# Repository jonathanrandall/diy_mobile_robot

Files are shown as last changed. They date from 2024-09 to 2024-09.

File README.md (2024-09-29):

# DIY Mobile Robotics Platform:
The video instructions are [here](https://youtu.be/9S9H8HX5MNA). <br/>
The regression used to calibrate the stereo camera is in the file __points_regression.ods__. <br/>
The fritzing diagram for the pcb is in __esp32_motor_control.fzz__ <br/>
The gerber files for the pcb are in __gerber_esp32_motor_control__ <br/>
The code is in [robot_software](https://github.com/jonathanrandall/diy_mobile_robot/tree/main/robot_software). <br/>
Robot software depends on [cvzone library](https://github.com/cvzone/cvzone).

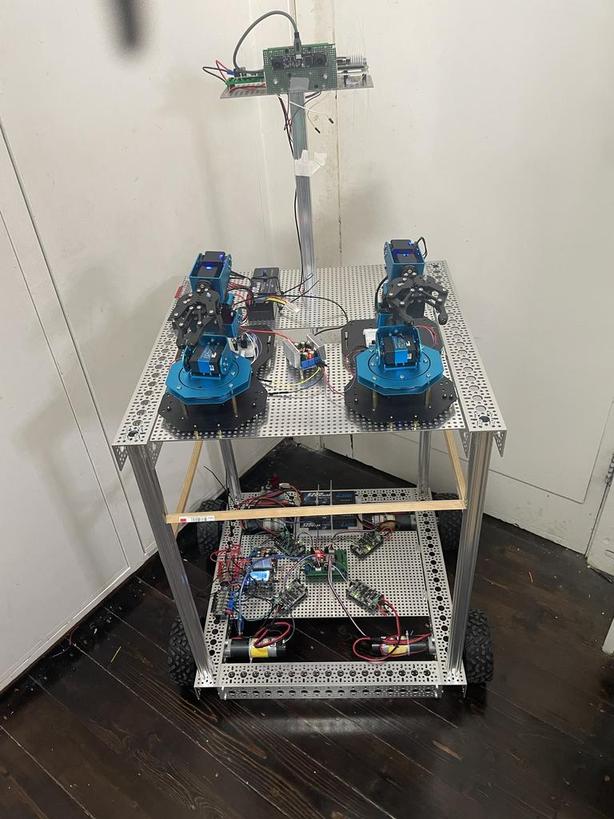
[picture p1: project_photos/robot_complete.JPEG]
the robot


# Assemble the Frame and Motors.

__Screw Drivers and Hex Keys__<br/>
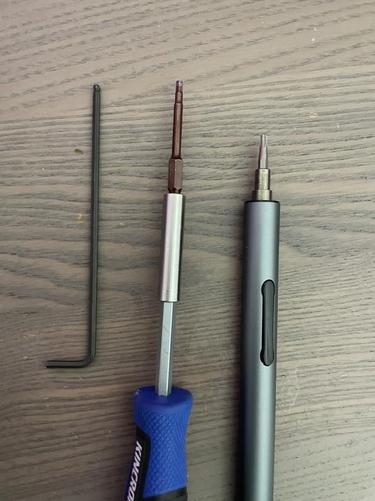
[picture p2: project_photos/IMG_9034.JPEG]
screw drivers
 <br/>
The M4 socket head screws require a 3mm drive size. It is recommended to get the __Wera Tools 3mm Ball-End Hex-Plus L-Key__ (SKU: 5027104001). This will make building much easier, since it can access screws in awkward places. The drivers I used are pictured below.

__Step 1: Build the base of the frame:__<br/>
Note: robot upside down in picutre, so base is at the top. <br/>
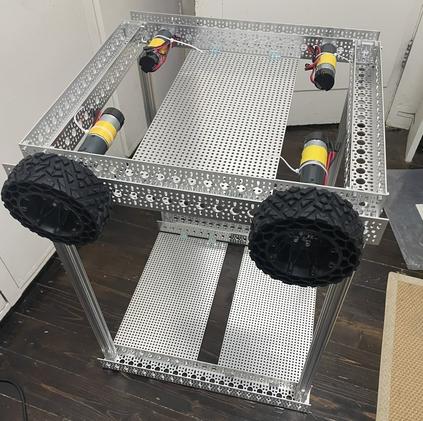
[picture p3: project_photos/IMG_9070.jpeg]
robot frame
<br/>
<ins>parts list for base</ins>
* 2 X 432mm 1120 Series U-Channel (SKU: 1120-0017-0432)
* 2 X 528mm 1120 Series U-Chaneel (SKU: 1120-0021-0528)
* 4 X 1201 Series Quadblock pattern mount (SKU: 1201-0043-0002)
* 16 X 11mm M4 screws
* 16 X 8mm M4 screws
* 16 X 12mm M4 screws
* 4 X flanged ball bearing, 8mm REX ID x 14mm OD, 5mm thickness (SKU: 1611-0514-4008). Note ID is inner diameter and OD is outer diameter.
* 4 X 1320 Series hyper hub, 8mm REX Bore (SKU: 1310-0016-4008)
* 4 X Threaded Steel L-Bracket, 3 hole (SKU: 1147-0001-0003). Note there are four in each pack, so once pack.
* 1 X 1116 Series Grid Plate, 29 x 53 Hole, 232 x 424mm (SKU: 1116-0232-0424)
* 24 X 6mm screws (can also use 8mm if you run out, but 6mm is preferred).
* 5204 Series Yellow  Jacket Planetary Gear Motor, 80mm Lenght 8mm REX shart, 117 RPM (SKU: 5204-8002-0051). Note, this is the long shaft motor. If you use the shorter shaft, you will need a coupler and a shaft to attach to the wheel. This can be quite fiddly and adds to the cost. Also I'm using the 117 RPM motor, which is not fast but has good torque. My aim is to handle a payload of up to 50kg on a 30 degree incline. According to my calculations, this should handle that quite well, but might struggle witht he 223 RMP version.
* 4 X 1109 Series goRail, 624mm lenghth (SKU: 1109-0024-0624). 

<ins>Assembly of base</ins>
1. Attach the quadblocks to the end of the shorter U-channels (432mm) with the 11mm screws. Mounting the quadblocks on the shorter channels will result in the base being a square. Each channel is 48mm wide, so the base will be (432 +48 +48) = 528mm. Note, you can use different sized U-Channels, depending on what you need. I've chosen theses sizes to bring it into line with the Stanford Mobile Aloha robot. This build is on the wider end of what I would normally do.<br/> 
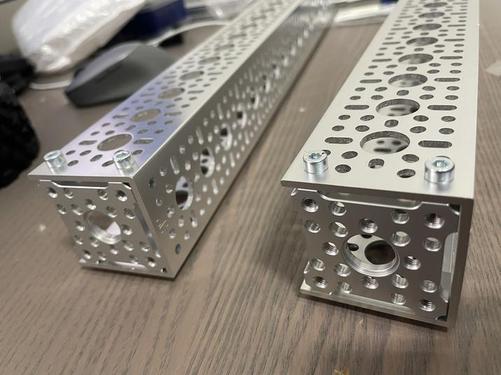
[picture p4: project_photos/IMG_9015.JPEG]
Quad Blocks

2. Attach the two 432mm at right angles with the 528mm channels, using the 8mm screws to connect, to make a square shape (see picture).<br/>
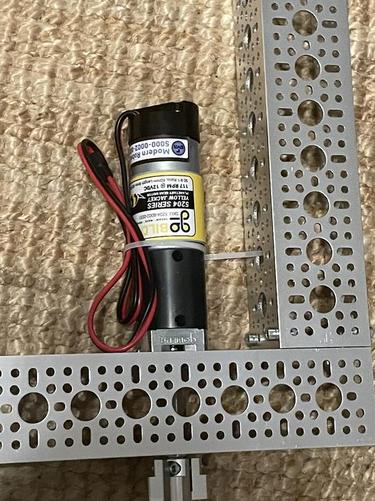
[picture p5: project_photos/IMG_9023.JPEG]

3. Attach the motors to the side of the frame. You can 10mm to 12mm screws for this. I've attached mine to the fourth hole down. There are lots of diagrams on the gobilda page for attaching the motors to channel. Make sure the motor's power wires and encoder plug are facing upwards, so they are easy to access from the top. <br/>
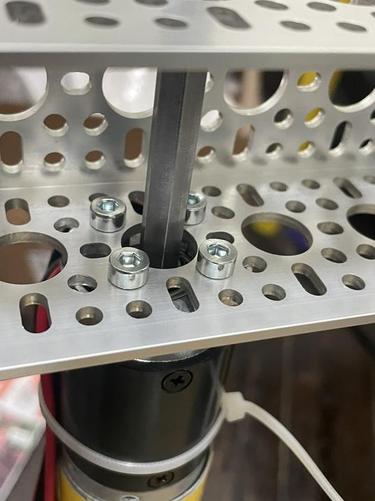
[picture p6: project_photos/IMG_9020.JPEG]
motor attach

4. Place the bearing,spacer and hyperhub on the end of the motor shaft and push down so that everything is nice and snug. Tighten the pinch screws on the hyperhub. Don't place the wheels on yet. They will get in the way.<br/>
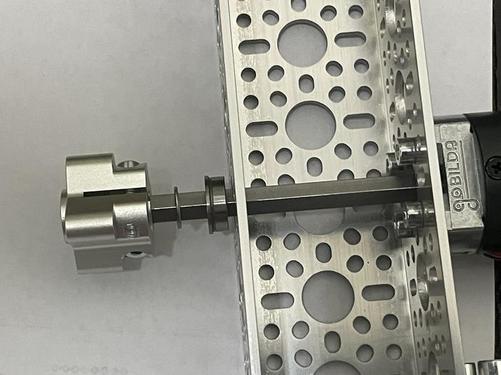
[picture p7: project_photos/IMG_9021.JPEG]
bearing attach

5. Attach the goRail to the corners of the base with the 12mm M4 screws (or 10mm is ok as well), so they are standing verticle. They have threaded holes, which will line up with the holes on the U-Channel. When you attach a goRail, do not tighten the screws until all four have been placed, otherwise you risk cross-threading. I'm using 624mm goRail. You can use up to 1200mm. You can adjust the height of the goRail without changing anything else. If you adjust the dimensions of the U-Channel, the grid plates will also need to be adjusted.<br/>
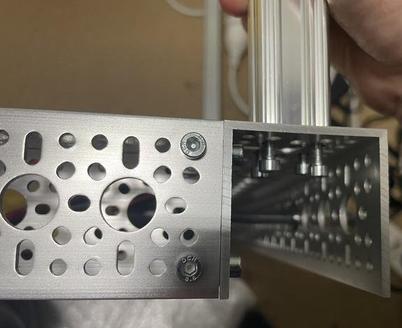
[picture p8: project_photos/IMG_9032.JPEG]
gorail attach
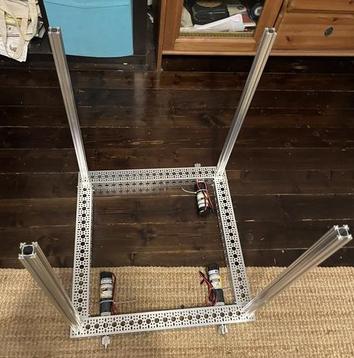
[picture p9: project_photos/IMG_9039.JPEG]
gorail
 
6. Attach the L-Brackets, with the 6mm M4 screws, to each of the U-Channels that the motors are on. They should be attached off centre becasue this is where you are going to mount the grid plate.<br/>
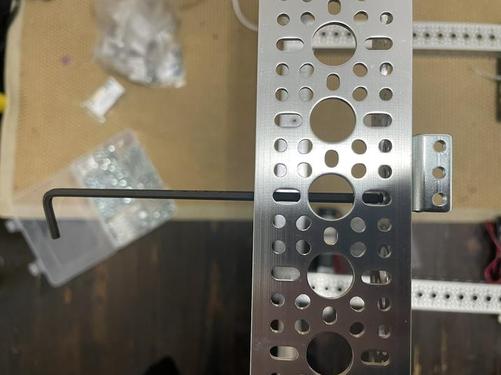
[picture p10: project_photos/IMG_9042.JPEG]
L brackets attach

7. Mount the grid plate on the L-Brackets with the 6mm M4 screws.<br/>
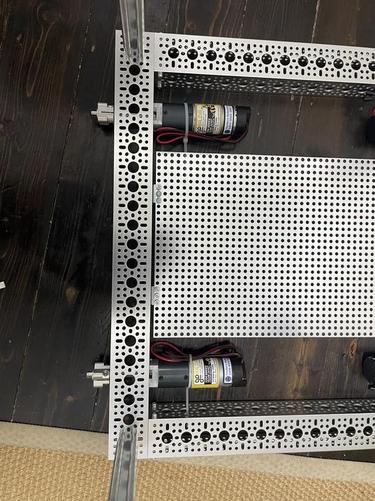
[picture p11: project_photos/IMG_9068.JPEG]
grid plate attach


__Step 2: Build the top of the frame:__

<ins>parts list</ins>
* 2 X 528mm 1120 Series U-Chaneel (SKU: 1120-0021-0528)
* 2 X 1116 Series Grid Plate, 29 x 53 Hole, 232 x 424mm (SKU: 1116-0232-0424)
* 8 X Threaded Steel L-Bracket, 3 hole (SKU: 1147-0001-0003). Note there are four in each pack, so two packs.
* 48 X 6mm M4 screws (can also use 8mm if you run out, but 6mm is preferred).

<ins>Assembly of top of the frame</ins>
1. Attach the 4 L-Brackets to the edge of each of the U-Channels, so that the U-Channel is like an upside down U, and the bracket is flush with the top (see picture). Makes sure the L-Brackets are spaced, so that you can attach the grid plates. Don't put any in the middle of the channel.
2. Once you have all L-brackets attached line up the two U-channels with the brackets facing each other and put the grid plates on, so that the two U-Channels are held together with the grid plates. Make sure the grid plates are attached along the short edge (see pictures). So the long edge is connecting the two U-Channels. Everything is measured out so it fits perfectly on the top of the robot.<br/>
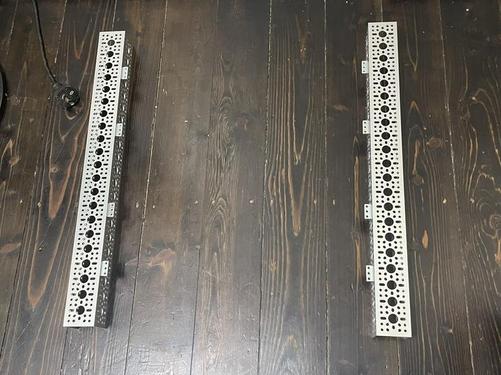
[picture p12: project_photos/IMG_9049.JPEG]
top grid
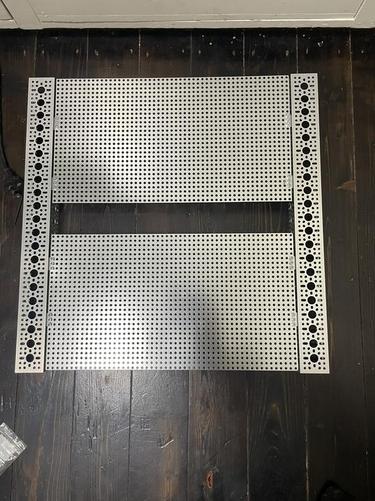
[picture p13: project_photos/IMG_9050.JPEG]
top grid 2
 

__Step 3: Attach the top of the frame:__

<ins>parts list</ins>
* 16 X 12mm M4 screws. Can use anywhere from 10mm to 12mm for this step, depedending on what you have. I mixed it up a bit because I was running out of 12mm screws.

<ins>Finish assembly</ins?
1. Line up the threaded holes in the GoRail with the holes in the corner of the top of the frame.
2. Fix on with the chosen screws.<br/>
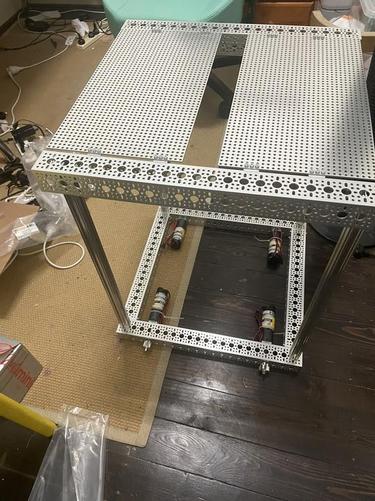
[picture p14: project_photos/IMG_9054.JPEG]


__Step 4: Attach the wheels:__

Put the wheels on last, otherwise they get in the way when you're trying to screw on the other stuff.

<ins>parts list</ins>
* Four wheels. I'm using the Wasteland Wheel, 144mm Diameter, 52mm Width (SKU: 3616-0014-0144)
* 16 X 11mm M4 screws (can also use 10mm).
* 4 X washers

<ins>Assembly of wheels</ins>
1. Screw onto hyperhubs with 11mm screws and washers.<br/>
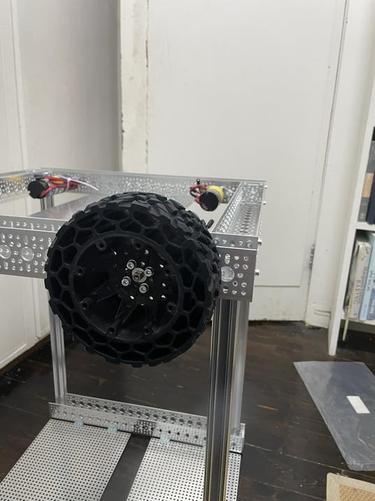
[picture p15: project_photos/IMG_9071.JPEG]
<br/>

# Assemble the Bottom Layer to get the robot driving
(Note: Also, need top battery for this)
The bottom layer of the robot contains the motor controllers, the esp32 a buck converter set to 12V and a buck converter set to 5V

### Parts list:
1. Cytron MD10C R3 motor controllers X 4. Or you can 2 X dual cytron dual motor drivers. I would recommend cytron if you want to use my code an wiring.
2. PCB or bread board. I printed up a PCB. The gerber files and fritzing files should be attached to this repo. I got this done at PCBWay.
3. ESP32: I'm using the 38 pin waveshare esp32. This has a thinner form factor than the ones you get off Amazon. My PCB design should also fit the fatter 38 pin esp32. I got it here https://www.waveshare.com/nodemcu-32s.htm
4. Nylon stand offs. I would get two packs of these.
5. 6S lipo battery or 2 X 3S lipo batteries. I used two 3S lip batteries in series. Also will need one 3S for the top.
6. Battery mount. I 3D printed mine. But you can make one out of lego, since the grid plates on the gobilda system line up with the lego grids, it is easy to drill holes to attach.
7. Four pin JST XH connectors. These are for the motor encoders. I used these from GoBilda. But you can use any you like. SKU: 3802-0910-0300
8. Bullet extenders (female) to connect the motor to the motor encoders. I used these from GoBilda. SKU:3800-0013-0300
9. Missile Switch. I used the missile switch to control the power to the motors because it's easy to turn off in a hurry, and i liked the look of it. I attached it with lego.
10. Buck converter for 5V. I'm using this one [here](https://www.amazon.com.au/gp/product/B08RBXCJCF/)
11. High current buck converter for 12V. I'm using [this one](https://www.amazon.com.au/gp/product/B08KXTV6RH/), which outputs 20A max. 
12. Terminal strips X 4 (two for the top and two for the bottom). I used terminal strips with plastic cover and sixe connections. Six is the minimum. Make sure you get the ones with the plastic cover because if you drop a screw driver or something on it, you can cause a short.
13. Fork lugs for connecting the wires to the terminal strips.
14. Red and Black wires. Make sure you use red for positive and black for ground.
15. Dupont femal to male jumper wires X 14. Two to connect the pcb to grnd and positive. And 12 to connect the motor controllers to the PCB.

## Connection Tables

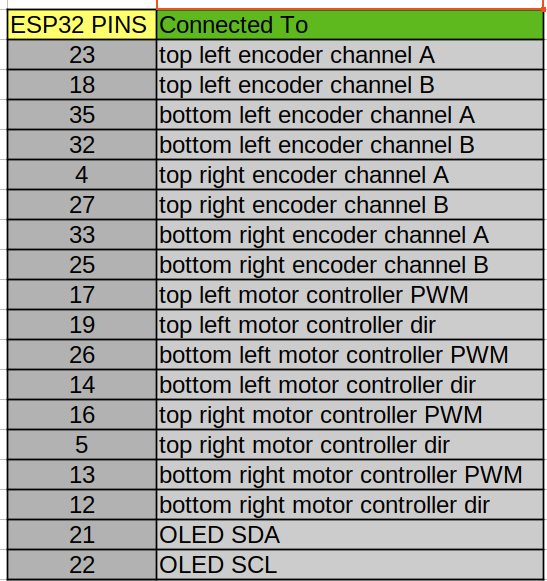
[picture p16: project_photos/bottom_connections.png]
ESP32 connections
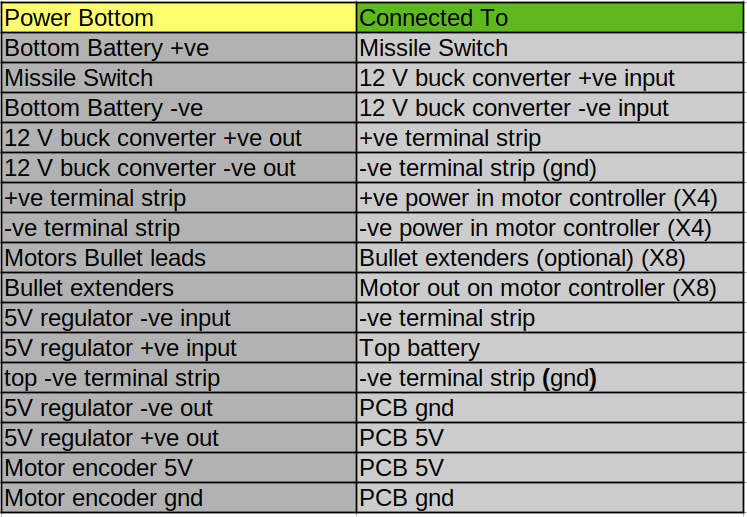
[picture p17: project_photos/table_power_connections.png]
bottom power connections
 

## Steps to assemble bottom of robot

__Bottom of the robot:__ Connect all parts as shown in the picture. I've screwed my motor controllers on diagonally because that was the only way I could get the standoffs to line up with the holes. Only the two diagonal standoffs are attached to the gridplate. And make connections as in above tables <br/>
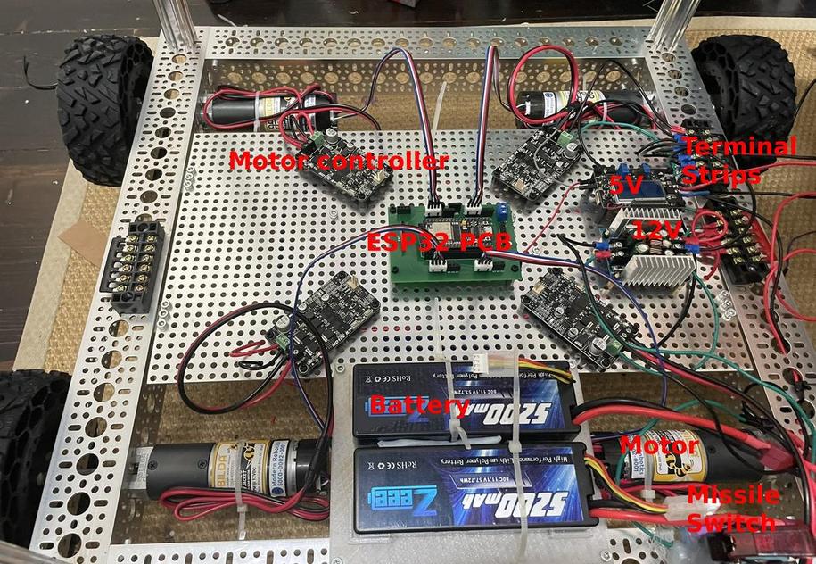
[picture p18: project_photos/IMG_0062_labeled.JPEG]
labeled bottom
 <br/>

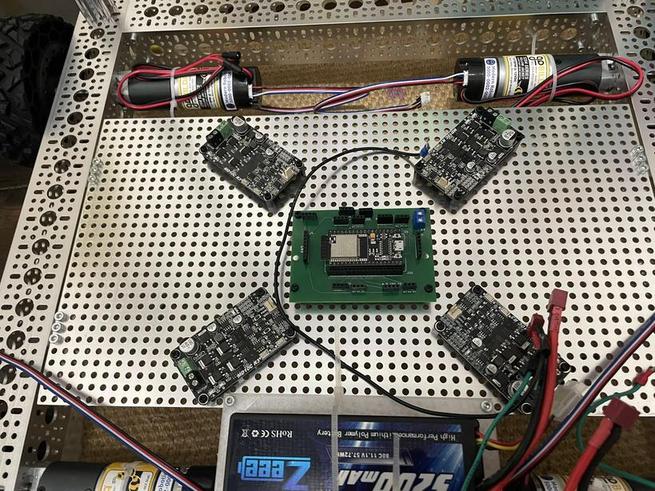
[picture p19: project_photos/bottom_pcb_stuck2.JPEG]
motor controller and pcb
 <br/>

# Assemble the Top of the robot

The top of the robot contans the raspberry pi 5, stereo camera and robot arms. Assemble as shown in the picutres.<br/> 
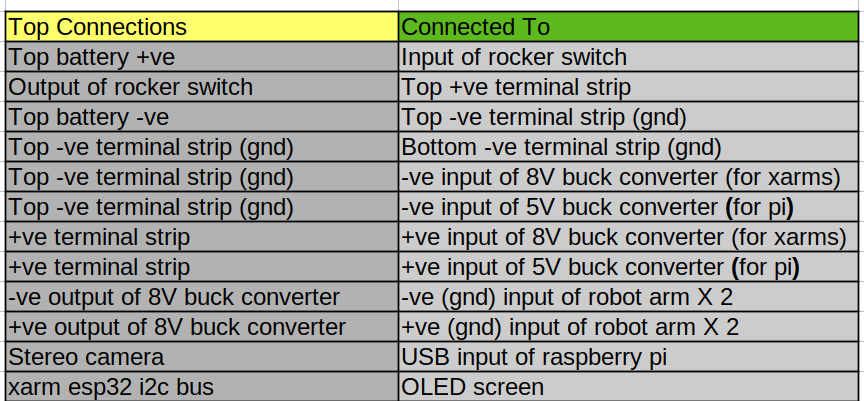
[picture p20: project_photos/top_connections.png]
Connecctions
 <br/>
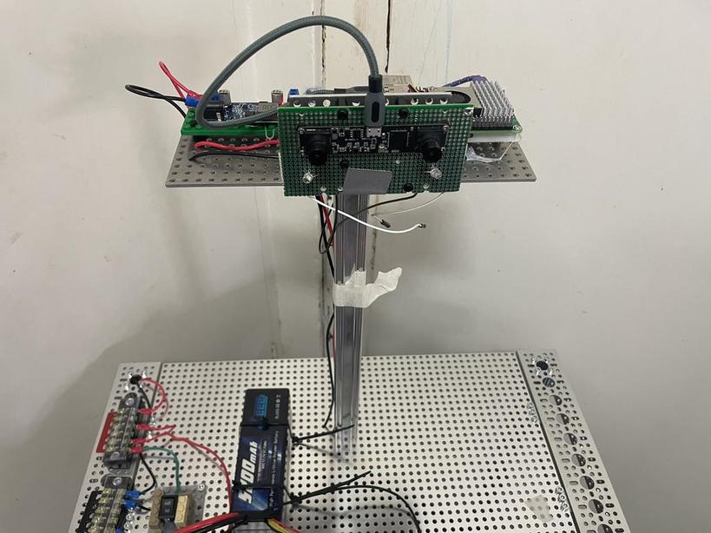
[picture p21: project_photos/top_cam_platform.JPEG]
This is the platform
 <br/>
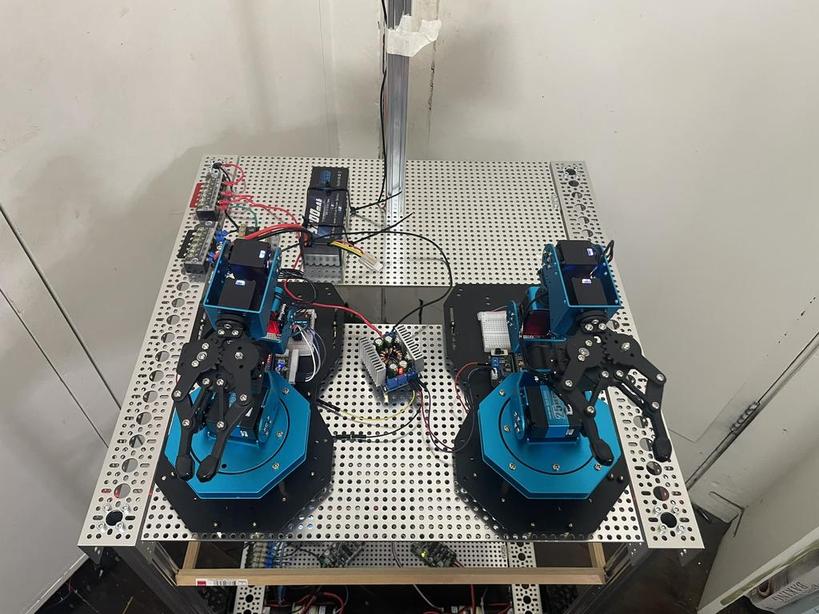
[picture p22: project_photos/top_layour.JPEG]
this is the top platform
 <br/>

### Parts list, electronics and robotics:
1. [__Hiwonder XARM esp32 X 2__](https://www.hiwonder.com/products/xarm-esp32)
2. __Raspberry pi 5.__
3. Raspberry pi 5 mount. I 3D printed [this one](https://www.printables.com/model/253933-simple-raspberry-pi-mount).
4. 3S battery.
5. __5A, 5V buck converter__ for raspberry pi (I used a non adjustable one). Make sure you get a good quality one, or else the pi won't start. I used __[tunghey 2Pack DC 9V 12V 24V to DC 5V 5A Buck Converter Module, 9-36V Step Down to USB 5V Transformer Dual Output Voltage Regulator Board](https://www.amazon.com.au/gp/product/B0D5V5YDC3/)__ from Amazon. The other alternative is to use a Waveshare UPS supply at 5V, but this is more expensive. I also tried an 8A buck converter but the pi wouldn't boot (probably because the voltage was a bit noisy?) and I tried a powerbank and the pi worked but with throttling on the CPU, which means it would run a bit slower. This is attached to the grid with a piece of lego, which is mounted on stand offs. The lego grid matches the goBilda grid plates, so it's easy to drill holes.
6. Adjustable Buck converter running at 8V to power the robot arms. I used this one: [DC5-30V to 1.25-30V Automatic Step DC-to-DC Power Converter UP/Down Converter Boost/Buck Voltage Regulator Module](https://www.amazon.com.au/gp/product/B08FXN9V68/), which is rated for high current and is fine with the robot arms, but didn't work with the pi.
7. __Stereo Camera__. I used [this one](https://www.amazon.com.au/gp/product/B07R8LQKV4/). Which is a Synchronized Dual Lens Stereo USB Camera 1.3MP HD 960P Webcam 3D VR Web Camera Module with 1/3 CMOS OV9715. Any stereo camera should work, but you need to make sure the left an right frames are synchronized, especially if the robot is moving.
8. Rocker switch.
9. Terminal strips X 4 (two for the top and two for the bottom). I used terminal strips with plastic cover and sixe connections. Six is the minimum. Make sure you get the ones with the plastic cover because if you drop a screw driver or something on it, you can cause a short.
10. Fork lugs to connect to the terminal strips.
11. Red and black wires (less than or equal 14 AWG).
12. Copper standoffs for XARM.
13. Nylong standoffs for 8V buck converter.
14. Male to male jumpber cables for connecting 8V buck converter to robot arm.

## structure parts:

__these parts will be used to mount the stereo camera an raspberry pi__
1. [1109 Series goRAIL](https://www.gobilda.com/1109-series-gorail-336mm-length/) (336mm Length). This is the neck (SKU: 1109-0024-0336).
2. [1116 Series Grid Plate](https://www.gobilda.com/1116-series-grid-plate-29-x-53-hole-232-x-424mm/) (29 x 53 Hole, 232 x 424mm). This is the platform to mount the pi on.
3. [1113 Series L-Channel](https://www.gobilda.com/1113-series-l-channel-1-hole-48mm-length/) (1 Hole, 48mm Length). This will connect the perf board that the camera is on to the grip plate to it is at right angles (SKU: 1113-0001-0048).
4. perf board. The camera is mounted on a perf board. This was from an old project, but it turned out quite nicely because the holes in the perf board lined up with the mounting holes in the camera.

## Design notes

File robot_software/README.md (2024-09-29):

### This directory contains the software for the robot.

__There are three directories for sofware__

1. [esp32_stuff/esp32_controls](https://github.com/jonathanrandall/diy_mobile_robot/tree/main/robot_software/esp32_stuff/esp32_controls): This directory contains the code for the esp32 that goes on the esp32 that is on the bottom level of the robot. thi is written in Platform IO. The code broadcasts a webpage over a local wifi network. So you need to input the wifi ssid and password for this to work. Also, the routines to move the robot a certain distance are on free rtos. I have them threaded so they won't block the commands set to the robot. This means, the "STOP" won't be blocked and I don't have to implement an emergency stop with an interrupt. It also means I can interrupt the robot with other commands if neeed be.
2. [rpi_stuff](https://github.com/jonathanrandall/diy_mobile_robot/tree/main/robot_software/rpi_stuff): This directory contains the python code that is running on the raspberry pi.
   - The hand_distance_measure code is used for calibrating the stereo cameras.
   - The pose_estimation_measure broadcasts the stereo image over the network (for me this is address http://rpi5.local, but for you, you will need to replace the name rpi5 with the name you gave your raspberry pi when you flashed the operating system).
3. [wifi_xarm_control_v2](https://github.com/jonathanrandall/diy_mobile_robot/tree/main/robot_software/wifi_xarm_control_v2):This is the micropython code that is flashed to the esp32 on the [hiwonder robot arms](https://www.hiwonder.com/products/xarm-esp32).

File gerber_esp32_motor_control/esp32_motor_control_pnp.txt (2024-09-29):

*Pick And Place List
*Company=
*Author=
*eMail=
*
*Project=esp32_motor_control
*Date=16:10:51
*CreatedBy=Fritzing 0.9.6b..
*
*
*Coordinates in mm, always center of component
*Origin 0/0=Lower left corner of PCB
*Rotation in degree (0-360, math. pos.)
*
*No;Value;Package;X;Y;Rotation;Side;Name
1;;;3.25944;-9.17593;0;Bottom;Hole6
2;;screwterminal-3.5mm-2_lock;89.0072;-57.3359;90;Bottom;GND
3;;;3.25944;-65.0559;0;Bottom;Hole4
4;;;92.1594;-9.17593;0;Bottom;Hole1
5;;THT;87.0794;-38.3859;0;Bottom;J5
6;;THT;76.9194;-57.4359;90;Bottom;gnd pwm dir
7;;THT;51.5194;-19.3359;90;Bottom;J11
8;;THT;38.8194;-65.0559;90;Bottom;5V
9;;THT;51.5194;-62.5159;90;Bottom;GND
10;;;92.1594;-32.0359;0;Bottom;Hole3
11;;;92.1594;-65.0559;0;Bottom;Hole2
12;;;12.0888;-61.3061;0;Bottom;TXT2
13;;THT;65.4894;-57.4359;90;Bottom;A B GND 5V
14;;THT;12.1494;-62.5159;90;Bottom;J12
15;;THT;46.4394;-9.17593;90;Bottom;gnd pwm dir
16;;;91.2865;-51.4828;0;Bottom;TXT1
17;;;3.25944;-32.0359;0;Bottom;Hole5
18;;THT;68.0294;-9.17593;90;Bottom;A B GND 5V
19;;THT;79.4594;-9.17593;90;Bottom;gnd pwm dir
20;;THT;35.0094;-57.4359;90;Bottom;A B GND 5V
21;;;7.33911;-38.1437;90;Bottom;TXT1
22;;THT;10.8794;-38.3859;0;Bottom;J4
23;;THT;35.0094;-9.17593;90;Bottom;A B GND 5V
24;;THT;51.5194;-44.7359;90;Bottom;
25;;THT;46.4394;-57.4359;90;Bottom;gnd pwm dir
26;;;51.2219;-34.7992;0;Bottom;U1

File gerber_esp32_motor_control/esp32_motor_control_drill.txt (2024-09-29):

; NON-PLATED HOLES START AT T1
; THROUGH (PLATED) HOLES START AT T100
M48
INCH
T1C0.165354
T100C0.038000
T101C0.038779
T102C0.047244
%
T1
X001283Y012612
X036283Y012612
X001283Y025612
X001283Y003612
X036283Y025612
X036283Y003612
T100
X016283Y007612
X015283Y007612
X019283Y022612
X017283Y003612
X012283Y003612
X014283Y007612
X004283Y014612
X034283Y017612
X024283Y022612
X027283Y022612
X020283Y007612
X012283Y007612
X031283Y022612
X020283Y024612
X018283Y003612
X028283Y007612
X019283Y024612
X017283Y007612
X025283Y007612
X025283Y003612
X011283Y007612
X014283Y025612
X003283Y024612
X011283Y017612
X029283Y022612
X013283Y003612
X021283Y024612
X012283Y017612
X025283Y017612
X015283Y003612
X013283Y022612
X020283Y017612
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

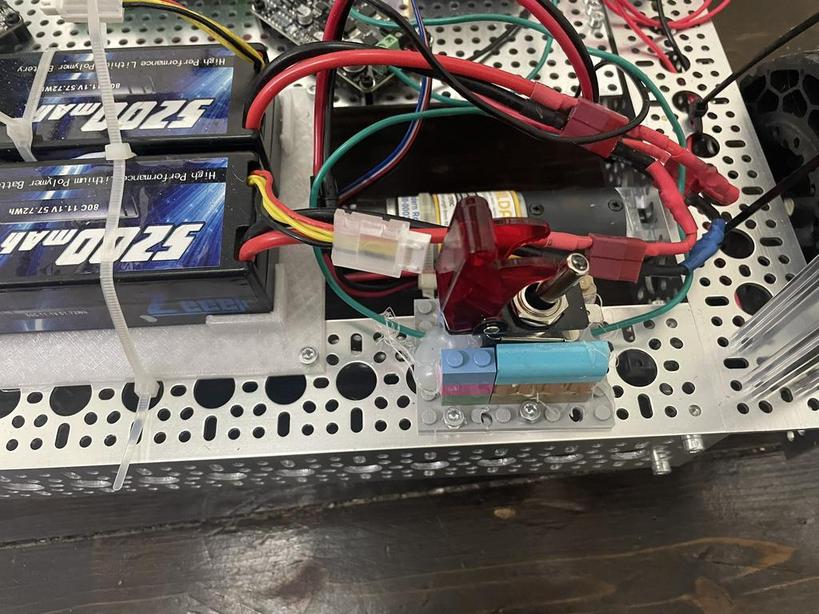
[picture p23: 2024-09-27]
project_photos/missile_switch.JPEG

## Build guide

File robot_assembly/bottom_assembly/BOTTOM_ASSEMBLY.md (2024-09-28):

# Bottom of robot
The bottom layer of the robot contains the motor controllers, the esp32 a buck converter set to 12V and a buck converter set to 5V

## Parts list:
1. Cytron MD10C R3 motor controllers X 4. Or you can 2 X dual cytron dual motor drivers. I would recommend cytron if you want to use my code an wiring.
2. PCB or bread board. I printed up a PCB. The gerber files and fritzing files should be attached to this repo. I got this done at PCBWay.
3. ESP32: I'm using the 38 pin waveshare esp32. This has a thinner form factor than the ones you get off Amazon. My PCB design should also fit the fatter 38 pin esp32. I got it here https://www.waveshare.com/nodemcu-32s.htm
4. Nylon stand offs. I would get two packs of these.
5. 6S lipo battery or 2 X 3S lipo batteries. I used two 3S lip batteries in series. Also will need one 3S for the top.
6. Battery mount. I 3D printed mine. But you can make one out of lego, since the grid plates on the gobilda system line up with the lego grids, it is easy to drill holes to attach.
7. Four pin JST XH connectors. These are for the motor encoders. I used these from GoBilda. But you can use any you like. SKU: 3802-0910-0300
8. Bullet extenders (female) to connect the motor to the motor encoders. I used these from GoBilda. SKU:3800-0013-0300
9. Missile Switch. I used the missile switch to control the power to the motors because it's easy to turn off in a hurry, and i liked the look of it. I attached it with lego.
10. Buck converter for 5V. I'm using this one [here](https://www.amazon.com.au/gp/product/B08RBXCJCF/)
11. High current buck converter for 12V. I'm using [this one](https://www.amazon.com.au/gp/product/B08KXTV6RH/), which outputs 20A max. 
12. Terminal strips X 4 (two for the top and two for the bottom). I used terminal strips with plastic cover and sixe connections. Six is the minimum. Make sure you get the ones with the plastic cover because if you drop a screw driver or something on it, you can cause a short.
13. Fork lugs for connecting the wires to the terminal strips.
14. Red and Black wires. Make sure you use red for positive and black for ground.
15. Dupont femal to male jumper wires X 14. Two to connect the pcb to grnd and positive. And 12 to connect the motor controllers to the PCB.

## Connection Tables

ESP32 connections bottom power connections

## Steps to assemble bottom of robot

__Bottom of the robot__<br/>
labeled bottom <br/>
The bottom of the robot contains motor controllers, motors, batteries, esp32, 5V & 12V regulators and terminal strips for power wires.

1. Screw on the PCB and the motor controllers. I've screwed my motor controllers on diagonally because that was the only way I could get the standoffs to line up with the holes. Only the two diagonal standoffs are attached to the gridplate <br/>
2. stuff
3. stuff
4. sst

motor controller and pcb <br/>

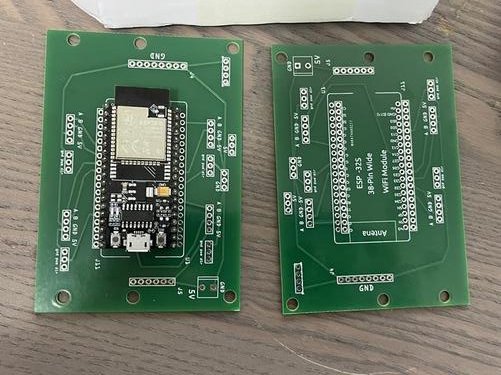
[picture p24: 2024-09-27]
project_photos/pcb_assemble.JPEG

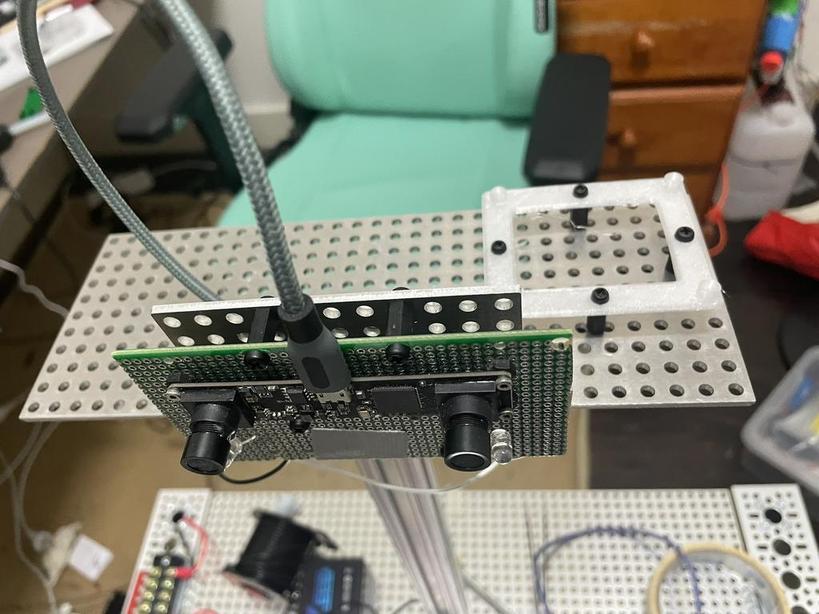
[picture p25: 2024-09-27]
project_photos/cam_assembly_front.JPEG

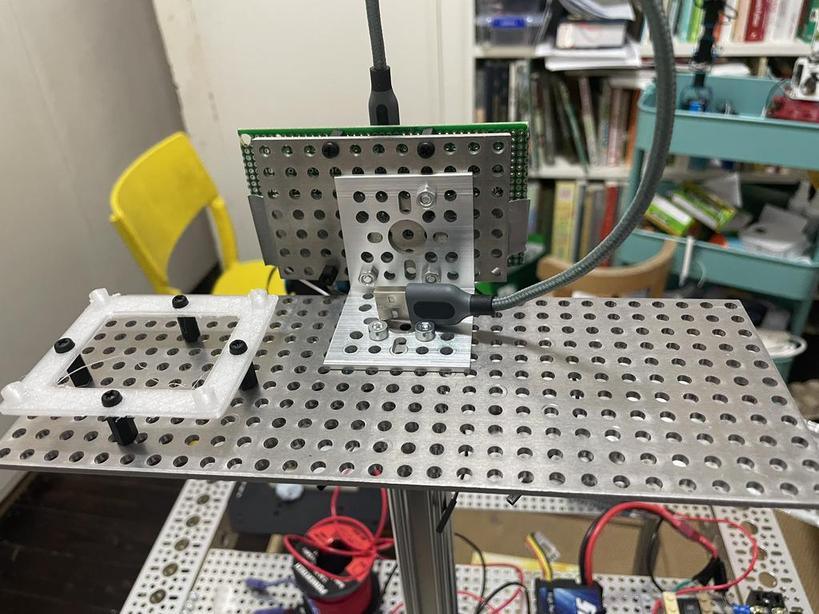
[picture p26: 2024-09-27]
project_photos/cam_assembly_back.JPEG

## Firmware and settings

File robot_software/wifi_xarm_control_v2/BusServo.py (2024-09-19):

from machine import Pin,UART
from micropython import const
import time, ustruct

SERVO_MOVE_TIME_WRITE       = const(1)
SERVO_MOVE_TIME_READ        = const(2)
SERVO_POS_READ              = const(28)
SERVO_MOVE_STOP             = const(12)
SERVO_ID_WRITE              = const(13)
SERVO_ID_READ               = const(14)

SERVO_ANGLE_OFFSET_ADJUST   = const(17)
SERVO_ANGLE_OFFSET_WRITE    = const(18)
SERVO_ANGLE_OFFSET_READ     = const(19)

SERVO_VIN_READ              = const(27)
SERVO_OR_MOTOR_MODE_WRITE   = const(29)
SERVO_LOAD_OR_UNLOAD_WRITE  = const(31)

have_got_servo_pos = {}

def get_low8_byte(data):
  return (data & 0xFF)

def get_high8_byte(data):
  return ((data>>8) & 0xFF)
  
def byte_to_hw(a, b):
  return (a | (b << 8))
  
  
class BusServo:
  def __init__(self, tx, rx, tx_en = None, rx_en = None):
    self.rx_buf = [0x55]
    self.isAutoEnableRT = False
    if tx_en == None:
      self.isAutoEnableRT = True
      
    if self.isAutoEnableRT == False:
      self.tx_en = Pin(tx_en, Pin.OUT)
      self.rx_en = Pin(rx_en, Pin.OUT)
      self.rx_enable()
    
    self.uart = UART(2, 115200, tx=tx, rx=rx)

  def rx_enable(self):
    if self.isAutoEnableRT == False:
      self.rx_en.value(1)
      self.tx_en.value(0)
  
  def tx_enable(self):
    if self.isAutoEnableRT == False:
      self.rx_en.value(0)
      self.tx_en.value(1)
    
  def check_sum(self, data):
    sum = 0
    for i in range(2,data[3] + 2):
      sum += data[i]
    sum = ~sum
    return (sum & 0xFF)
    
  def send_data(self, data):
    self.tx_enable()
    for d in data:
      self.uart.write(ustruct.pack('B',d))
    # time.sleep_us(10)
    if self.isAutoEnableRT == False:
      self.rx_en.value(1)
      self.tx_en.value(0)
    # self.rx_enable()
  def run(self, id, p, servo_run_time = 1000):
    tx_buf = [0x55,0x55]
    tx_buf.append(id)
    tx_buf.append(7)
    tx_buf.append(SERVO_MOVE_TIME_WRITE)
    tx_buf.append(get_low8_byte(p))
    tx_buf.append(get_high8_byte(p))
    tx_buf.append(get_low8_byte(servo_run_time))
    tx_buf.append(get_high8_byte(servo_run_time))
    tx_buf.append(self.check_sum(tx_buf))
    self.send_data(tx_buf)
  
  def run_mult(self, pp, servo_run_time):
    for p in enumerate(pp):
      self.run(p[0] + 1, p[1], servo_run_time)
   
  def run_add_or_dec(self, id, speed):
    try:
      pos = have_got_servo_pos[id]
    except:
      pos = self.get_position(id)
      if pos == False:
        return False

    pos += speed
    if pos < 0:pos = 0
    if pos > 1000:pos = 1000
    have_got_servo_pos[id] = pos
    self.run(id, pos, 20)
    return True
    
  def stop(self, id):
    tx_buf = [0x55,0x55]
    tx_buf.append(id)
    tx_buf.append(3)
    tx_buf.append(SERVO_MOVE_STOP)
    tx_buf.append(self.check_sum(tx_buf))
    self.send_data(tx_buf)

  def set_ID(self, old_id,new_id):
    tx_buf = [0x55,0x55]
    tx_buf.append(old_id)
    tx_buf.append(4)
    tx_buf.append(SERVO_ID_WRITE)
    tx_buf.append(new_id)
    tx_buf.append(self.check_sum(tx_buf))
    self.send_data(tx_buf)

  def get_ID(self, id):
    self.uart.read()
    tx_buf = [0x55, 0x55]
    tx_buf.append(id)
    tx_buf.append(3)
    tx_buf.append(SERVO_ID_READ)
    tx_buf.append(self.check_sum(tx_buf))
    self.send_data(tx_buf)

    time_now = time.ticks_ms()
    while self.uart.any() == 0:
      if time.ticks_ms() - time_now > 50:
        return False
    if self.servo_receive_handle():
      return self.rx_buf[5]
    return False

  def set_mode(self, id, mode, speed = 0):
    tx_buf = [0x55,0x55]
    tx_buf.append(id)
    tx_buf.append(7)
    tx_buf.append(SERVO_OR_MOTOR_MODE_WRITE)
    tx_buf.append(mode)
    tx_buf.append(0)
    tx_buf.append(get_low8_byte(speed))
    tx_buf.append(get_high8_byte(speed))
    tx_buf.append(self.check_sum(tx_buf))
    self.send_data(tx_buf)
    
  def load(self, id):
    tx_buf = [0x55,0x55]
    tx_buf.append(id)
    tx_buf.append(4)
    tx_buf.append(SERVO_LOAD_OR_UNLOAD_WRITE)
    tx_buf.append(1)
    tx_buf.append(self.check_sum(tx_buf))
    self.send_data(tx_buf)
    
  def unload(self, id):
    tx_buf = [0x55,0x55]
    tx_buf.append(id)
    tx_buf.append(4)
    tx_buf.append(SERVO_LOAD_OR_UNLOAD_WRITE)
    tx_buf.append(0)
    tx_buf.append(self.check_sum(tx_buf))
    self.send_data(tx_buf)
    
    
  def servo_receive_handle(self):
    frameStarted = False
    frameCount = 0
    dataCount = 0
    dataLength = 2
    self.rx_buf = [0x55]
    time_now = time.ticks_ms()
    while self.uart.any():
      buf = ustruct.unpack('B', self.uart.read(1))[0]
      time.sleep_us(100)
      if not frameStarted:
        if buf == 0x55:
          frameCount += 1
          if frameCount == 2:
            frameCount = 0
            frameStarted = True
            dataCount = 1
        else:
          frameStarted = False
          dataCount = 0
          frameCount = 0
        
      if frameStarted:
        self.rx_buf.append(buf)
        
        if dataCount == 3:
          dataLength = self.rx_buf[dataCount]
          if dataLength < 3 or dataLength > 7:
            dataLength = 2
            frameStarted = False
        dataCount += 1
        if dataCount == dataLength + 3:
          c = self.check_sum(self.rx_buf)
          if c == self.rx_buf[dataCount - 1]:
            return True
          return False
      if time.ticks_ms() - time_now > 1000:
        return False
    
  def get_position(self, id):
    self.uart.read()
    tx_buf = [0x55,0x55]
    tx_buf.append(id)
    tx_buf.append(3)
    tx_buf.append(SERVO_POS_READ)
    tx_buf.append(self.check_sum(tx_buf))
    
    self.send_data(tx_buf)
    
    time_now = time.ticks_ms()
    while self.uart.any() == 0:
      if time.ticks_ms() - time_now > 50:
        return False
    if self.servo_receive_handle():
      return ustruct.unpack('h', ustruct.pack('H', byte_to_hw(self.rx_buf[5], self.rx_buf[6])))[0]
    return False
  
  def get_positions(self):
    pos_ids = [1,2,3,4,5,6]
    positions = [self.get_position(id) for id in pos_ids]
    return positions
  
  def set_positions(self, goal_positions, servo_run_time):
    assert len(goal_positions) == 6
    for n, p in enumerate(goal_positions):
      self.run(id=n+1, p=p, servo_run_time=servo_run_time)
    

  def get_vin(self, id):
    self.uart.read()
    tx_buf = [0x55,0x55]
    tx_buf.append(id)
    tx_buf.append(3)
    tx_buf.append(SERVO_VIN_READ)
    tx_buf.append(self.check_sum(tx_buf))
    
    self.send_data(tx_buf)
    
    time_now = time.ticks_ms()
    while self.uart.any() == 0:
      if time.ticks_ms() - time_now > 50:
        return False
    if self.servo_receive_handle():
      return byte_to_hw(self.rx_buf[5], self.rx_buf[6])
    return False

  def adjust_offset(self, id,offset):
    tx_buf = [0x55,0x55]
    tx_buf.append(id)
    tx_buf.append(4)
    tx_buf.append(SERVO_ANGLE_OFFSET_ADJUST)
    tx_buf.append(offset)
    tx_buf.append(self.check_sum(tx_buf))
    self.send_data(tx_buf)

  def save_offset(self, id):
    tx_buf = [0x55,0x55]
    tx_buf.append(id)
    tx_buf.append(3)
    tx_buf.append(SERVO_ANGLE_OFFSET_WRITE)
    tx_buf.append(self.check_sum(tx_buf))
    self.send_data(tx_buf)

  def get_offset(self, id):
    self.uart.read()
    tx_buf = [0x55, 0x55]
    tx_buf.append(id)
    tx_buf.append(3)
    tx_buf.append(SERVO_ANGLE_OFFSET_READ)
    tx_buf.append(self.check_sum(tx_buf))
    self.send_data(tx_buf)

    time_now = time.ticks_ms()
    while self.uart.any() == 0:
      if time.ticks_ms() - time_now > 50:
        return False
    if self.servo_receive_handle():
      return ustruct.unpack('b',ustruct.pack('B',self.rx_buf[5]))[0]
    return False


# if __name__ == '__main__':
#   b = BusServo(tx=26, rx=35, tx_en=25, rx_en=12)
#   b.run(1,600)
  
#   print(b.get_position(2))

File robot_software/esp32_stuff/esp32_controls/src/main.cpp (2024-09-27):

#include <Arduino.h>
#include <WiFi.h>
#include <AsyncTCP.h>
#include <ESPAsyncWebServer.h>
#include "soc/soc.h"
#include "soc/rtc_cntl_reg.h"
#include "encoders_stuff.h"
#include "motor_ctrl_stuff.h"
#include "OLED_stuff.h"
#include "ssid_stuff.h"
#include "html_stuff.h"



// put function declarations here:


void setup() {
  WRITE_PERI_REG(RTC_CNTL_BROWN_OUT_REG, 0);
  Serial.begin(115200);
  init_wifi();
  start_server();
  init_encoders();
  robot_setup();

  left_motor_speed=106;
  right_motor_speed=106;

  unsigned long timer_strt;
  unsigned long timer_cur;
  timer_strt = millis();
  timer_cur = timer_strt;

  bool calib=false;
  if (calib){
    robot_fwd();

    while(millis()-timer_strt<2000){
      if(millis()-timer_cur > 300){
        timer_cur = millis();
        //print out pos*pule

        for (int i =0; i<4; i++){
          Serial.print("Motor: ");
          Serial.print(i); 
          Serial.print(", pulses: ");
          long enc = get_encoder_pos(i);
          float dist = ((float) enc )*pulse_dist;
          Serial.print(enc);
          Serial.print(", dist: ");
          Serial.println(dist);
        }
      }
    }
    robot_stop();
    // delay(500);
    emergency_stop=false;
    calibrate_motors(80);
    calibrate_motors(70);
    calibrate_motors(60);
    calibrate_motors(50);
    calibrate_motors(40);
    calibrate_motors(30);
    calibrate_motors(20);
    calibrate_motors(10);
  } //if calib
  emergency_stop=true;
  // move_robot_dist(2000.0);

  // robot_stop();

}

void loop() {
  // put your main code here, to run repeatedly:
}

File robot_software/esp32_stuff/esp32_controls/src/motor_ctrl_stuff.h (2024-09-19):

#ifndef MOTORS_STUFF_
#define MOTORS_STUFF_
#include <Arduino.h>
#include "encoders_stuff.h"

#define LEFT            0
#define RIGHT           1

// pins

#define RIGHT_MOTOR_PWM 16 //
#define RIGHT_MOTOR_DIR 5 //
#define LEFT_MOTOR_PWM 17  //
#define LEFT_MOTOR_DIR 19  //

//back motors (Back of board)

#define RIGHT_MOTOR_PWM2 13 //
#define RIGHT_MOTOR_DIR2 12 //
#define LEFT_MOTOR_PWM2 26 //
#define LEFT_MOTOR_DIR2 14 //

QueueHandle_t dist_queue = NULL;
QueueHandle_t dist_queue_int;
QueueHandle_t theta_queue;
QueueHandle_t theta_queue_int; //inetrrupt

TaskHandle_t move_dist_task;
TaskHandle_t move_theta_task;



bool emergency_stop = false;

uint8_t pwm_pins[] = {LEFT_MOTOR_PWM, LEFT_MOTOR_PWM2,RIGHT_MOTOR_PWM, RIGHT_MOTOR_PWM2};
uint8_t dir_pins[] = {LEFT_MOTOR_DIR, LEFT_MOTOR_DIR2,RIGHT_MOTOR_DIR, RIGHT_MOTOR_DIR2};


// pwm paramters
const int mtr_left_pwm_channel = 8;
const int mtr_right_pwm_channel = 4;
const int mtr_left_pwm2_channel = 5;
const int mtr_right_pwm2_channel = 6;
const int lresolution = 8;
const int freq = 4000;

const int pwm_channels[] = {mtr_left_pwm_channel,mtr_left_pwm2_channel,mtr_right_pwm_channel,mtr_right_pwm2_channel};


int left_motor_speed;
int left_motor_speed2;
int right_motor_speed;
int right_motor_speed2;

int motor_spds[] = {150,150,150,150};

int set_target_speed(float target, int motor, int init_spd);
void set_motor_speed_motor(uint8_t pwm_channel, uint8_t motor_dir, int spd);
void move_dist(void *params);
void move_theta(void *params);

void robot_setup()
{
  // Pins for Motor Controller
  pinMode(LEFT_MOTOR_DIR, OUTPUT);
  pinMode(LEFT_MOTOR_PWM, OUTPUT);
  pinMode(RIGHT_MOTOR_DIR, OUTPUT);
  pinMode(RIGHT_MOTOR_PWM, OUTPUT);
  pinMode(LEFT_MOTOR_DIR2, OUTPUT);
  pinMode(LEFT_MOTOR_PWM2, OUTPUT);
  pinMode(RIGHT_MOTOR_DIR2, OUTPUT);
  pinMode(RIGHT_MOTOR_PWM2, OUTPUT);

  // Motor uses PWM Channel 8
  ledcSetup(mtr_left_pwm_channel, freq, lresolution);
  ledcAttachPin(LEFT_MOTOR_PWM, mtr_left_pwm_channel);
  ledcWrite(mtr_left_pwm_channel, 0);

  ledcSetup(mtr_right_pwm_channel, freq, lresolution);
  ledcAttachPin(RIGHT_MOTOR_PWM, mtr_right_pwm_channel);
  ledcWrite(mtr_right_pwm_channel, 0);

  ledcSetup(mtr_left_pwm2_channel, freq, lresolution);
  ledcAttachPin(LEFT_MOTOR_PWM2, mtr_left_pwm2_channel);
  ledcWrite(mtr_left_pwm2_channel, 0);

  ledcSetup(mtr_right_pwm2_channel, freq, lresolution);
  ledcAttachPin(RIGHT_MOTOR_PWM2, mtr_right_pwm2_channel);
  ledcWrite(mtr_right_pwm2_channel, 0);

  dist_queue = xQueueCreate(7,sizeof(float));
  dist_queue_int = xQueueCreate(5,sizeof(bool));
  theta_queue = xQueueCreate(5,sizeof(float));
  theta_queue_int = xQueueCreate(5,sizeof(bool));

  xTaskCreatePinnedToCore(
    move_dist,
    "move_dist",
    5*1024,
    NULL,
    1,
    &move_dist_task,
    1);

  xTaskCreatePinnedToCore(
    move_theta,
    "move_theta",
    5*1024,
    NULL,
    1,
    &move_theta_task,
    1);
  
}

void calibrate_motors(float target_speed = 70)
{
  reset_encoders();

  //pid only use p

  // float traget_speed = 70;
  int point5_spd = 0;

  for (int i=0; i < 4; i++){
   point5_spd = set_target_speed(target_speed, i, 140);
   Serial.println("_________________________________");
   Serial.println("_________________________________");
   Serial.print("motor: ");
   Serial.print(i);
   Serial.print(", point5_spd: ");
   Serial.println(point5_spd);
   Serial.println("_________________________________");
   Serial.println("_________________________________");
  }
  

  //motor 1
  //start all motors
  //run for 5 seconds 
  //output encoder values.



}

int set_target_speed(float target, int motor, int init_spd=150){
  //pwm_pins
  //dir_pins
  unsigned long timer_strt;
  unsigned long timer_curr;

  int its = 0;
  
  uint8_t pwm_pin = pwm_pins[motor];
  uint8_t dir_pin = dir_pins[motor];

  const int pwm_channel = pwm_channels[motor];

  //run for 200ms, do encoder count

  
  float tol = 0.1;
  float error = 0.0;

  float speed = 0.0;

  long cnts_prev;
  long cnts;

  float Kp = 2.0;
  float Kd = 0.5;
  float Ki = 0.1;
  
  float iterm=0;
  float prev_error=0;
  float prev_speed;
  

  while(!emergency_stop && abs(speed-target)>tol){
    timer_strt = millis();
    cnts_prev = get_encoder_pos(motor);

    set_motor_speed_motor((uint8_t) pwm_channel, dir_pin, init_spd);

    while(millis()-timer_strt < 50){

    }

    
    
    cnts = get_encoder_pos(motor);

    speed = ((float) abs(cnts -cnts_prev))*pulse_dist*1000/((float) millis()-timer_strt);
    if (its==0) prev_speed = speed;  //initialise previous speed

    Serial.print("motor: ");
    Serial.print(motor);
    Serial.print(", speed: ");
    Serial.print(speed);
    Serial.print(", init_spd: ");
    Serial.print(init_spd);

    error = target-speed;

    // iterm += Ki*error;
    iterm = Ki*prev_error; //using momentum for the i-term instead.
    
    Serial.print(", error: ");
    Serial.println((int) ((error)*Kp+Kd*(speed-prev_speed)+iterm));
    init_spd += (int) (error*Kp+Kd*(speed-prev_speed)+iterm);
    // init_spd -= (int) (Kd*(speed-prev_speed));

    if (init_spd > 255){
      init_spd=255;
      Serial.println("speed maximised");
      // break;
    } 

    its++;
    if(its>10) break;

    prev_speed=speed;
    prev_error = error;

  }

  set_motor_speed_motor((uint8_t) pwm_channel, dir_pin, 0);

  return init_spd;

}

void set_robot_target_speed(float target, int spd){
  bool fwd = true;
  unsigned long timer_strt;
  unsigned long timer_curr;

  int its = 0;
  
  // uint8_t pwm_pin = pwm_pins[motor];
  // uint8_t dir_pin = dir_pins[motor];

  // const int pwm_channel = pwm_channels[motor];

  //run for 200ms, do encoder count

  
  float tol = 0.2;
  float error = 0.0;

  float speed = 0.0;

  long cnts_prev;
  long cnts;

  float Kp = 2.0;
  float Kd = 0.5;
  float Ki = 0.1;
  
  float iterm=0;
  float prev_error=0;
  float prev_speed;

  if (spd < 0)
  {
    spd = -spd;
    fwd = false;
  }
  if (spd > 255)
    spd = 255;

  

}

void set_motor_speed_motor(uint8_t pwm_channel, uint8_t motor_dir, int spd){
  //for single motor
  bool fwd = true;
  

  if (spd < 0)
  {
    spd = -spd;
    fwd = false;
  }
  if (spd > 255)
    spd = 255;

  digitalWrite( motor_dir, fwd ? HIGH : LOW);
  ledcWrite(pwm_channel,spd);

}
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

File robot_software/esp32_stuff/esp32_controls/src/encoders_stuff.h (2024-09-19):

#ifndef ENCODERS_STUFF_
#define ENCODERS_STUFF_

// wheel encoder interrupts
#include <Arduino.h>

#define encoder0PinA 23      // encoder top left
#define encoder0PinB 18

#define encoder1PinA 35     // encoder bottom left
#define encoder1PinB 32


#define encoder2PinA 4      // encoder top right
#define encoder2PinB 27

#define encoder3PinA 33     // encoder bottom right
#define encoder3PinB 25

volatile long encoder0Pos = 0;    // encoder 1 top left
volatile long encoder1Pos = 0;    // encoder 2 bottom left
volatile long encoder2Pos = 0;    // encoder 3 top right
volatile long encoder3Pos = 0;    // encoder 4 bottom right

const float ppr = 1425.1; //pulses per revolution
const float wheel_diameter = 13.7;//14.4;//cm
const float pi = 3.14159265359;
const float circum = wheel_diameter*pi; //cm
const float pulse_dist = circum/ppr;
const float robot_width = 60.0; //cm

const float turning_circle = robot_width*pi;

const float one_m = 100.0/pulse_dist; //number of pulses to travel 1m

void IRAM_ATTR doEncoderA();
void IRAM_ATTR doEncoderB();
void IRAM_ATTR doEncoderC();
void IRAM_ATTR doEncoderD();
void IRAM_ATTR doEncoderE();
void IRAM_ATTR doEncoderF();
void IRAM_ATTR doEncoderG();
void IRAM_ATTR doEncoderH();

void reset_encoders(){
  encoder0Pos = 0;    // encoder 1
  encoder1Pos = 0;    // encoder 2
  encoder2Pos = 0;    // encoder 3
  encoder3Pos = 0;    // encoder 4
}

void init_encoders(){
  pinMode(encoder0PinA, INPUT_PULLUP);    // encoder pins
  pinMode(encoder0PinB, INPUT_PULLUP);

  pinMode(encoder1PinA, INPUT_PULLUP); 
  pinMode(encoder1PinB, INPUT_PULLUP);

  pinMode(encoder2PinA, INPUT_PULLUP);    // encoder pins
  pinMode(encoder2PinB, INPUT_PULLUP);

  pinMode(encoder3PinA, INPUT_PULLUP); 
  pinMode(encoder3PinB, INPUT_PULLUP);


  attachInterrupt(encoder0PinA, doEncoderA, CHANGE);
  attachInterrupt(encoder0PinB, doEncoderB, CHANGE); 

  attachInterrupt(encoder1PinA, doEncoderC, CHANGE);
  attachInterrupt(encoder1PinB, doEncoderD, CHANGE); 

  attachInterrupt(encoder2PinA, doEncoderE, CHANGE);
  attachInterrupt(encoder2PinB, doEncoderF, CHANGE); 

  attachInterrupt(encoder3PinA, doEncoderG, CHANGE);
  attachInterrupt(encoder3PinB, doEncoderH, CHANGE);

  reset_encoders();
}

void IRAM_ATTR doEncoderA(){  

  // look for a low-to-high on channel A
  if (digitalRead(encoder0PinA) == HIGH) { 
    // check channel B to see which way encoder is turning
    if (digitalRead(encoder0PinB) == LOW) {  
      encoder0Pos = encoder0Pos + 1;         // CW
    } 
    else {
      encoder0Pos = encoder0Pos - 1;         // CCW
    }
  }
  else   // must be a high-to-low edge on channel A                                       
  { 
    // check channel B to see which way encoder is turning  
    if (digitalRead(encoder0PinB) == HIGH) {   
      encoder0Pos = encoder0Pos + 1;          // CW
    } 
    else {
      encoder0Pos = encoder0Pos - 1;          // CCW
    }
  }
 
}

void IRAM_ATTR doEncoderB(){  

  // look for a low-to-high on channel B
  if (digitalRead(encoder0PinB) == HIGH) {   
   // check channel A to see which way encoder is turning
    if (digitalRead(encoder0PinA) == HIGH) {  
      encoder0Pos = encoder0Pos + 1;         // CW
    } 
    else {
      encoder0Pos = encoder0Pos - 1;         // CCW
    }
  }
  // Look for a high-to-low on channel B
  else { 
    // check channel B to see which way encoder is turning  
    if (digitalRead(encoder0PinA) == LOW) {   
      encoder0Pos = encoder0Pos + 1;          // CW
    } 
    else {
      encoder0Pos = encoder0Pos - 1;          // CCW
    }
  }
  

}

// ************** encoder 2 *********************

void IRAM_ATTR doEncoderC(){  

  // look for a low-to-high on channel A
  if (digitalRead(encoder1PinA) == HIGH) { 
    // check channel B to see which way encoder is turning
    if (digitalRead(encoder1PinB) == LOW) {  
      encoder1Pos = encoder1Pos + 1;         // CW
    } 
    else {
      encoder1Pos = encoder1Pos - 1;         // CCW
    }
  }
  else   // must be a high-to-low edge on channel A                                       
  { 
    // check channel B to see which way encoder is turning  
    if (digitalRead(encoder1PinB) == HIGH) {   
      encoder1Pos = encoder1Pos + 1;          // CW
    } 
    else {
      encoder1Pos = encoder1Pos - 1;          // CCW
    }
  }
 
}

void IRAM_ATTR doEncoderD(){  

  // look for a low-to-high on channel B
  if (digitalRead(encoder1PinB) == HIGH) {   
   // check channel A to see which way encoder is turning
    if (digitalRead(encoder1PinA) == HIGH) {  
      encoder1Pos = encoder1Pos + 1;         // CW
    } 
    else {
      encoder1Pos = encoder1Pos - 1;         // CCW
    }
  }
  // Look for a high-to-low on channel B
  else { 
    // check channel B to see which way encoder is turning  
    if (digitalRead(encoder1PinA) == LOW) {   
      encoder1Pos = encoder1Pos + 1;          // CW
    } 
    else {
      encoder1Pos = encoder1Pos - 1;          // CCW
    }
  }
  

}

void IRAM_ATTR doEncoderE(){  

  // look for a low-to-high on channel A
  if (digitalRead(encoder2PinA) == HIGH) { 
    // check channel B to see which way encoder is turning
    if (digitalRead(encoder2PinB) == LOW) {  
      encoder2Pos = encoder2Pos + 1;         // CW
    } 
    else {
      encoder2Pos = encoder2Pos - 1;         // CCW
    }
  }
  else   // must be a high-to-low edge on channel A                                       
  { 
    // check channel B to see which way encoder is turning  
    if (digitalRead(encoder2PinB) == HIGH) {   
      encoder2Pos = encoder2Pos + 1;          // CW
    } 
    else {
      encoder2Pos = encoder2Pos - 1;          // CCW
    }
  }
 
}

void IRAM_ATTR doEncoderF(){  

  // look for a low-to-high on channel B
  if (digitalRead(encoder2PinB) == HIGH) {   
   // check channel A to see which way encoder is turning
    if (digitalRead(encoder2PinA) == HIGH) {  
      encoder2Pos = encoder2Pos + 1;         // CW
    } 
    else {
      encoder2Pos = encoder2Pos - 1;         // CCW
    }
  }
  // Look for a high-to-low on channel B
  else { 
    // check channel B to see which way encoder is turning  
    if (digitalRead(encoder2PinA) == LOW) {   
      encoder2Pos = encoder2Pos + 1;          // CW
    } 
    else {
      encoder2Pos = encoder2Pos - 1;          // CCW
    }
  }
  

}

// ************** encoder 2 *********************
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

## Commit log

2024-09-17 parts list
    [order_from_gobilda.xlsx]
2024-09-19 Update and rename README.md to FRAME_README.md
2024-09-22 3d printer files
    [Raspberry_Pi_Mount_V1.stl, battery_holderv2-Body.stl, battery_holderv2.FCStd]
2024-09-22 esp32 files
2024-09-22 Update FRAME_README (copy).md
